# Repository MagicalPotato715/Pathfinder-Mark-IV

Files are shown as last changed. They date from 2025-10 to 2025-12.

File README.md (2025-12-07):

# Pathfinder-Mark-IV
**IMPORTANT FOR REVIEWERS**: 
 - 1. The PCB price *really* is at the lowest it could possibly be, it's not possible to lower the price OR try to find a cheaper fab, I already thoroughly went through this with the reviewer @technical_ and he said that it's acceptable.
 - 2. The BOM is already optimized, and NO the parts on Aliexpress and Digikey cannot be sourced from LCSC (technically, LCSC does *sell* the terminal block, but the one seller's out of stock and has been for a while).
 - 3. This is NOT similar to Mk-III in ANY way aside from the fact that it's a hexapod. (if you reviewed it you'd know that) The entire system is completely different. Mk-III was a Nucleo Shield that used a 7.4v lipo battery connected to 3 buck converters directly connected to passives, that was basically it. However, Mk-IV is an on-board, Teensy, with a 6.6v Li-Fe Battery connected to a terminal-rocker switch system, with a back side I2C expander with 8 Tof Sensors.

If you don't believe me, ask @technical_, @NotARoomba, or @Tanook

What: Mark IV will be the fourth generation of my hexapod line: Pathfinder (not to be confused with the Hack Club YSWS). Mark IV will feature major consistency improvements to Mark III (mainly just not featuring buck converters). Additionally, Mark IV has an I2C expander connected to 8 ToF sensors that should allow the finished robot to have some form of autonomous movement.

Note: This project primarily focuses on the PCB of the Mark IV, as the body has already been printed, so it's a secondary focus (however, design tweaks may still be made to it).

Why: I began Pathfinder a year ago after my physics teacher encouraged me to join my school's science fair. I had always had an idea for a spider robot that I kept at the back of my mind, but this pushed me to bring it to life. Over the next few weeks, I poured hours every day into learning more about mechanical and electrical engineering. I also sought mentorship from the UC Berkeley Engineering Department and got connected with a Mech E & EECS graduate student. Mark I of Pathfinder, a simple prototype/proof of concept, was churned out after 2 weeks, just in time for my district's science fair to win me 2nd place. Mark II was developed a few weeks later for the regional science fair, and it featured my very first PCB a simple wire connector that I created using Onboard. Mark III was developed in the months after the science fair. I attempted to create a Hexpod orders of magnitude larger, with a system heavily centered on the PCB (I developed this PCB with Highway). However, when I finally got the PCB, soldered all of the components, and plugged it in, the core of the design: one of 3 buck converters to take 15 amps of power from the 7.4v battery to the 18 servo motors, blew up; ending Mark III. I developed Mark IV to continue on and actualize Pathfinder.

3D Model (Chassis):
Screenshot 2025-11-23 at 9 35 25 PM
Screenshot 2025-11-23 at 9 35 42 PM
Screenshot 2025-11-23 at 9 37 38 PM

3D Model (PCB in Kicad):

Screenshot 2025-11-23 at 9 38 09 PM
Screenshot 2025-11-23 at 9 38 37 PM
Screenshot 2025-11-23 at 9 38 54 PM

PCB Layout:

F. Cu
Screenshot 2025-11-23 at 9 46 05 PM
In1. Cu
Screenshot 2025-11-23 at 9 46 23 PM
In2. Cu
Screenshot 2025-11-23 at 9 46 39 PM
B. Cu
Screenshot 2025-11-23 at 9 46 55 PM

PCB Schematic:
Screenshot 2025-11-23 at 9 47 49 PM

|Name |Amount|Unit Cost|Unit Size|Total |FIELD6 |
|---|---|---|---|---|---|
|3.3v Zener Diode |1 |0.74 |20 |0.74  |https://www.lcsc.com/product-detail/C7441074.html?s_z=n_1N4728A |
|SMD Capacitor 10uf 0805 |2 |0.2 |20 |0.2 |https://www.lcsc.com/product-detail/C15850.html?s_z=n_SMD%2520Capacitor%25200805%252010uf |
|Header 1x3 M |18 |0.81 |20 |0.81  |https://www.lcsc.com/product-detail/C2937625.html?s_z=n_2.54mm%2520header |
|Header 1x5 F |9 |0.58 |20 |0.58  |https://www.lcsc.com/product-detail/C492404.html?s_z=n_2.54mm |
|SMD LED |20 |0.48 |50 |0.48  |https://www.lcsc.com/product-detail/C25170728.html |
|SMD Resistor 510ohm 0805 |19 |0.43 |50 |0.43  |https://www.lcsc.com/product-detail/C2828857.html?s_z=n_0805%2520LED |
|Servo Motors |6 |35.26 |4 |70.52 |https://www.aliexpress.us/item/3256806709778108.html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 |
|Li-Fe Battery 6.6v 3000mah |2 |19.32 |1 |38.64 |https://www.aliexpress.us/item/3256807464251198.html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|
|T-Plug M |2 |1.67 |1 |3.34  |https://www.aliexpress.us/item/3256806654144826.html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 |
|Metal Horn |18 |9.99 |15 |19.98 |https://www.amazon.com/Comimark-15Pcs-Metal-Disc-Arm25T-MG996R-RoWTUS/dp/B0855Q36Q3 |
|Buck Converter |1 |9.59 |5 |9.59  |https://www.amazon.com/dp/B0B779ZYN1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 |
|Terminal Block |2 |0.78 |1 |1.56  |https://www.digikey.com/en/products/detail/same-sky-formerly-cui-devices/TB005-762-02BE/10064113 |
|SMD Capacitor 0.1uf 0603 |3 |0.58 |100 |0.58  |https://www.lcsc.com/product-detail/C48579279.html?s_z=n_capacitor%25200603%2520100nf |
|THT Resistor 5k |1 |2.42 |100 |2.42  |https://www.aliexpress.us/item/3256806020720362.html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 |
|THT Resistor 4.7k |2 |2.37 |100 |2.37  |https://www.aliexpress.us/item/3256806020720362.html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 |
|Electrolytic Capacitor 1500uf|2 |0.6 |5 |0.6 |https://www.lcsc.com/product-detail/C233123.html?s_z=n_capacitor%25200603%2520100nf |
|Teensy 4.1 |1 |29.6 |1 |29.6  |https://www.digikey.com/en/products/detail/sparkfun-electronics/20359/16688101 |
|nRF24L01 |1 |5.19 |5 |5.19  |https://www.aliexpress.us/item/3256807013648418.html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 |
|PCA9548ADB |1 |1.38 |1 |1.38  |https://www.lcsc.com/product-detail/C2860563.html?s_z=n_PCA9548ADB |
|SMD Resistor 10k 0805 |18 |0.19 |100 |0.19  |https://www.aliexpress.us/item/3256804579227354.html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 |
|BNO055 |1 |26.9 |1 |26.9  |https://www.aliexpress.us/item/3256809169239048.html?gatewayAdapt=glo2usa |
|Rocker Switch |1 |7.39 |12 |7.39  |https://www.aliexpress.us/item/3256806293672719.html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 |
|JLCPCB |1 |74.42 |5 |74.42 | |
|Price Without Taxes/Shipping | | |Total =  |297.91| |

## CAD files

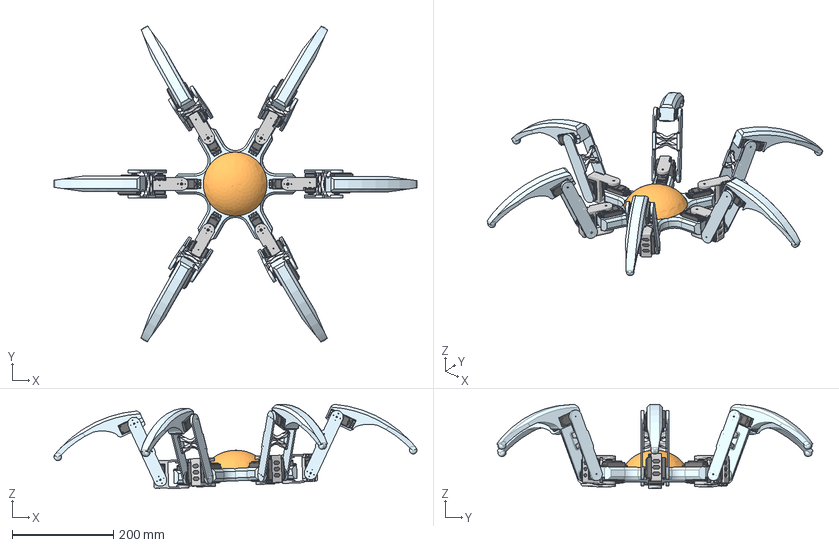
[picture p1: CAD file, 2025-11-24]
CAD models/Leg Assembly.step
717.0 x 624.6 x 166.9 mm
Case x 54
arm_round x 18
Output Shaft x 18

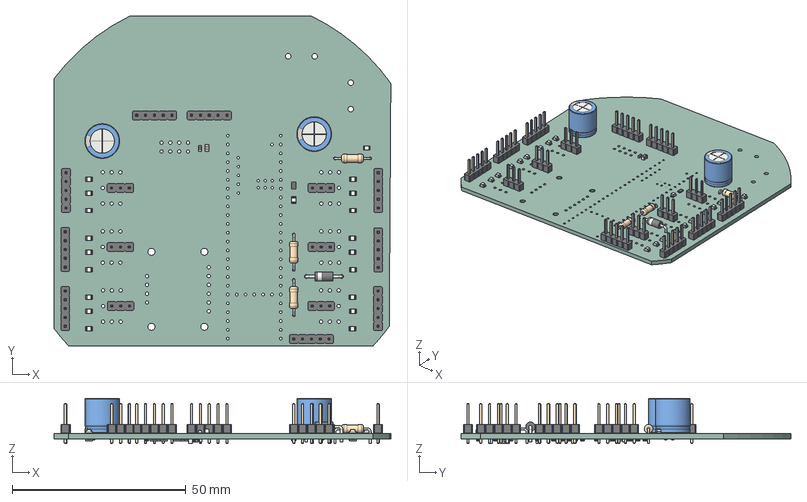
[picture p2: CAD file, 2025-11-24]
PF MKIV PCB Files/PF Mark IV.step
96.9 x 95.0 x 13.0 mm
C_0805_2012Metric x 2
LED_0805_2012Metric x 20
PinHeader_1x05_P2.54mm_Vertical x 9
R_0805_2012Metric x 39
PinHeader_1x03_P2.54mm_Vertical x 6
C_0603_1608Metric x 3
R_Axial_DIN0207_L6.3mm_D2.5mm_P10.16mm_Horizontal x 3
CP_Radial_D10.0mm_P5.00mm x 2
D_DO-41_SOD81_P10.16mm_Horizontal
PF Mark IV_PCB

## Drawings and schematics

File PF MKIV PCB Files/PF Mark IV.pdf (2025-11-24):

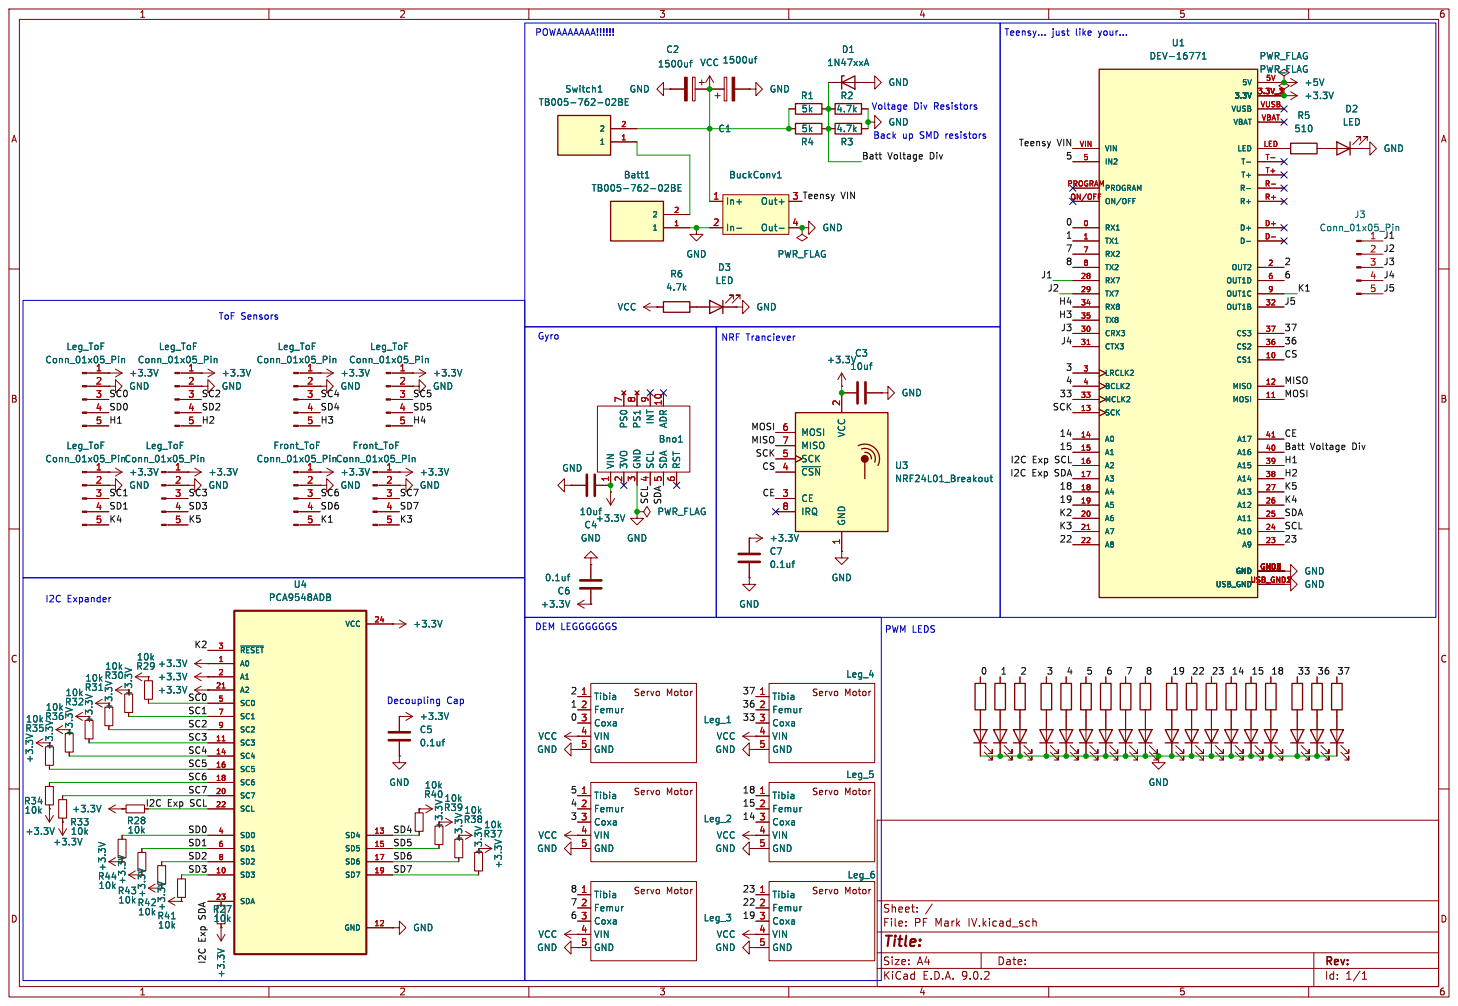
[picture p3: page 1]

Leg_4 Tibia 1 Femur 2 Coxa 3 VIN 4 GND 5 VCC GND

Servo Motor Tibia 1 Femur 2 Coxa 3 VIN 4 GND 5

Leg_5 Tibia 1 Femur 2 Coxa 3 VIN 4 GND 5 VCC GND

Leg_2 Tibia 1 Femur 2 Coxa 3 VIN 4 GND 5

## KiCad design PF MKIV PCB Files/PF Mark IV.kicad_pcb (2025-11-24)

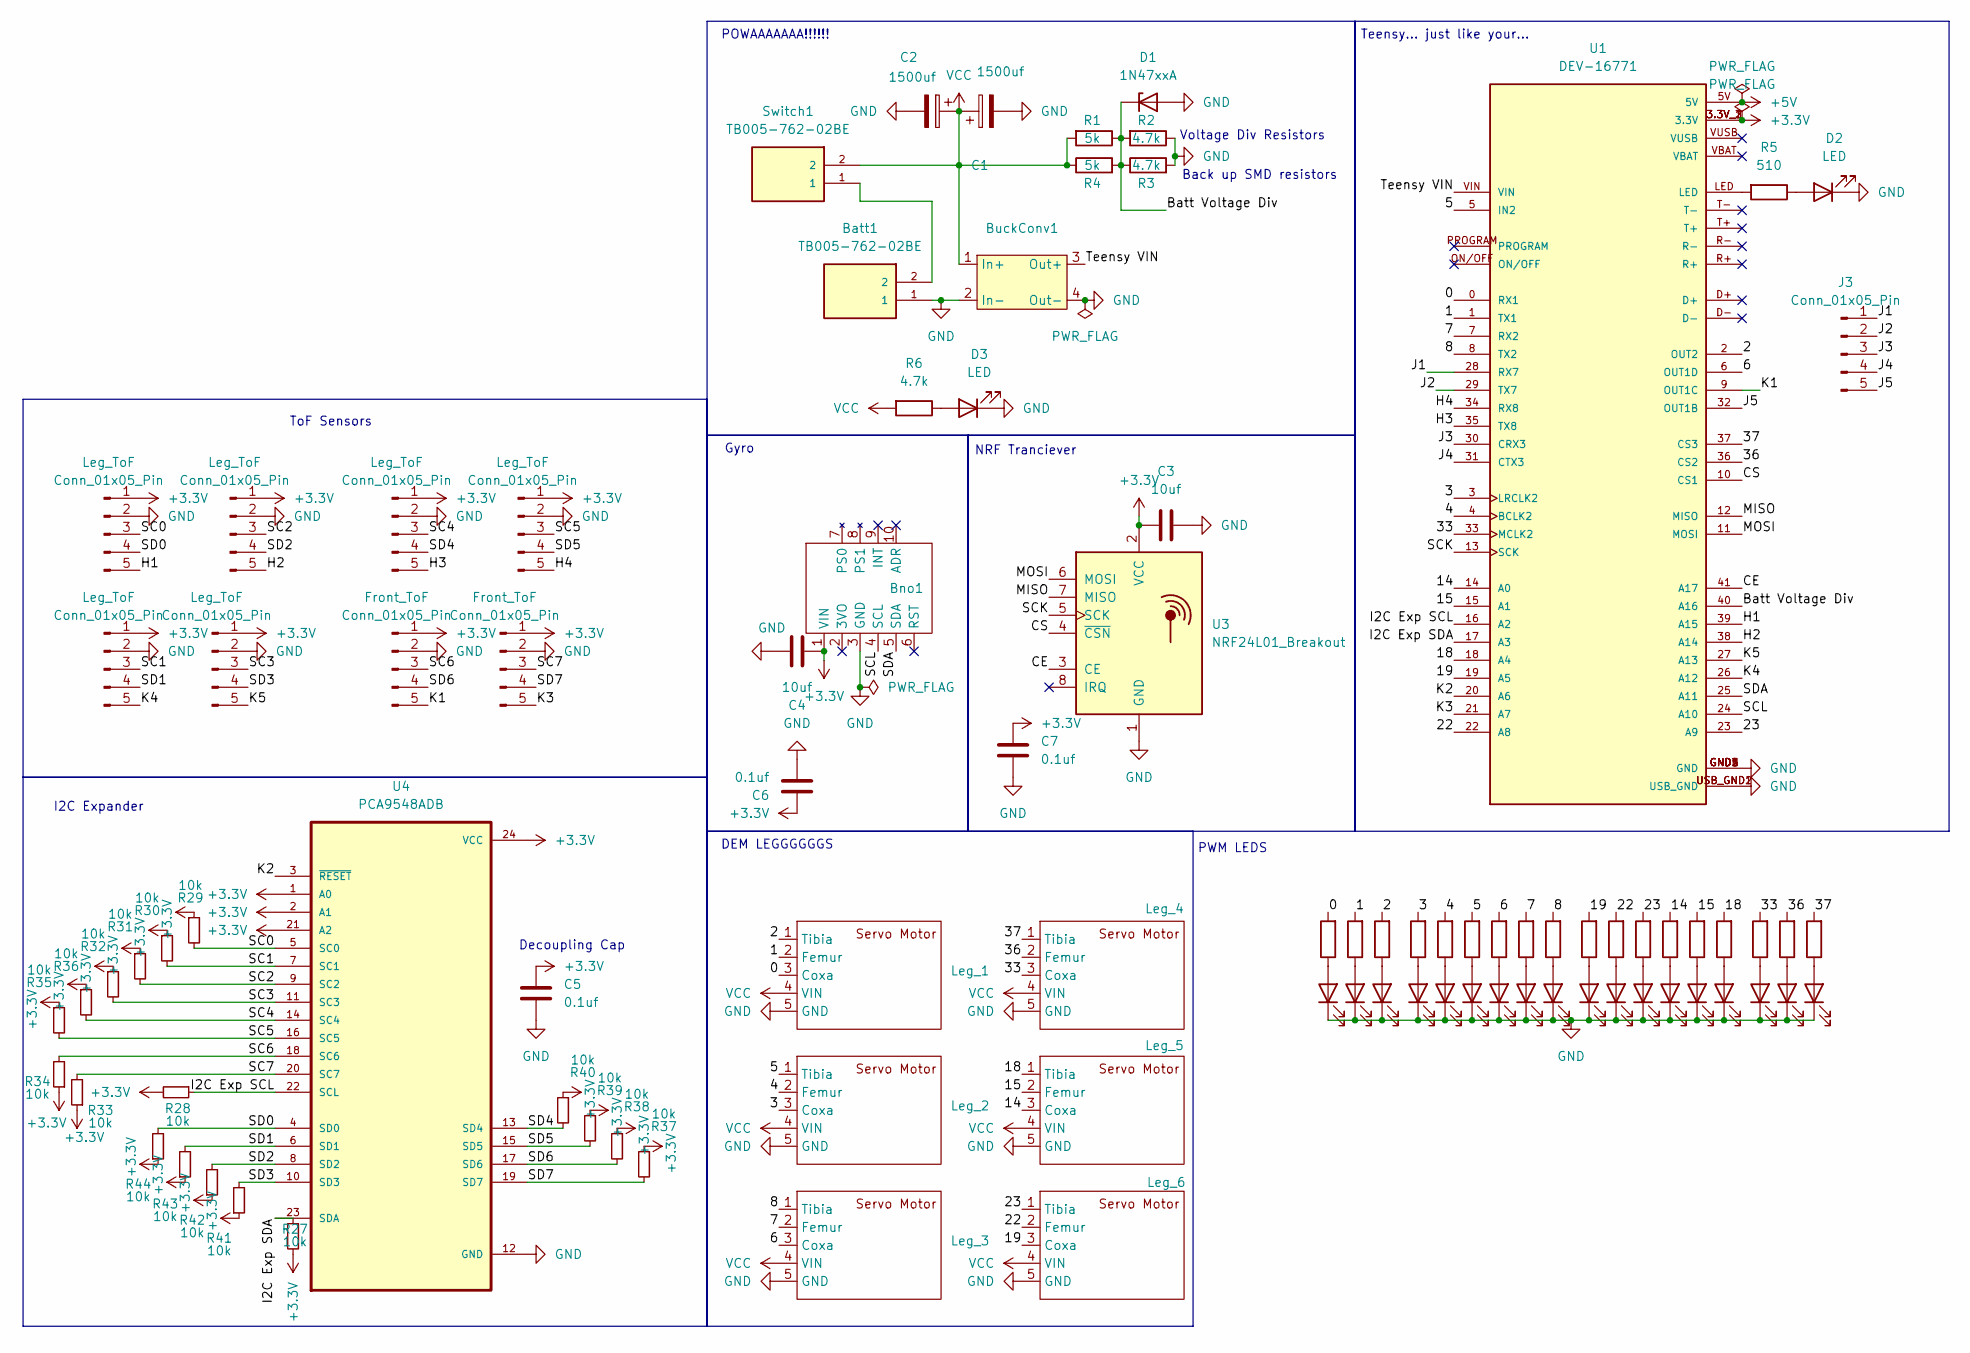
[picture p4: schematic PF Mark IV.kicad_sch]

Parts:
Batt1: TB005-762-02BE; CUI_TB005-762-02BE
Bno1: BNO055
BuckConv1: Buck Converter 5V MP1584EN
C1, C2: 1500uf; CP_Radial_D10.0mm_P5.00mm
C3, C4: 10uf; C_0805_2012Metric_Pad1.18x1.45mm_HandSolder
C5, C6, C7: 0.1uf; C_0603_1608Metric_Pad1.08x0.95mm_HandSolder
D1: 1N47xxA; D_DO-41_SOD81_P10.16mm_Horizontal
D2, D3, D4, D5, D6, D7, D8, D9, D10, D11, D12, D13, D14, D15, D16, D17, D18, D19, D20, D21: LED; LED_0805_2012Metric_Pad1.15x1.40mm_HandSolder
Front_ToF: Conn_01x05_Pin; PinHeader_1x05_P2.54mm_Vertical
J3: Conn_01x05_Pin; PinHeader_1x05_P2.54mm_Vertical
Leg_1, Leg_2, Leg_3, Leg_4, Leg_5, Leg_6: Leg_Servo
Leg_ToF: Conn_01x05_Pin; PinHeader_1x05_P2.54mm_Vertical
R1: 5k; R_Axial_DIN0207_L6.3mm_D2.5mm_P10.16mm_Horizontal
R2, R6: 4.7k; R_Axial_DIN0207_L6.3mm_D2.5mm_P10.16mm_Horizontal
R3: 4.7k; R_0805_2012Metric_Pad1.20x1.40mm_HandSolder
R4: 5k; R_0805_2012Metric_Pad1.20x1.40mm_HandSolder
R5, R7, R8, R9, R10, R11, R12, R13, R14, R15, R16, R17, R18, R19, R20, R21, R22, R23, R24: 510; R_0805_2012Metric_Pad1.20x1.40mm_HandSolder
R27, R28, R29, R30, R31, R32, R33, R34, R35, R36, R37, R38, R39, R40, R41, R42, R43, R44: 10k; R_0805_2012Metric_Pad1.20x1.40mm_HandSolder
Switch1: TB005-762-02BE; CUI_TB005-762-02BE
U1: DEV-16771; MODULE_DEV-16771; PARTREV 4.1
U3: NRF24L01_Breakout; nRF24L01_Breakout
U4: PCA9548ADB; SOP65P780X200-24N

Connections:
+3.3V: Bno1.1 (VIN), C3.1, C4.1, C5.1, C6.1, C7.1, Front_ToF.1, Leg_ToF.1, R27.2, R28.2, R29.1, R30.1, R31.1, R32.1, R33.1, R34.1, R35.1, R36.1, R37.1, R38.1, R39.1, R40.1, R41.1, R42.1, R43.1, R44.1, U1.3.3V_1 (3.3V), U1.3.3V_2 (3.3V), U1.3.3V_3 (3.3V), U3.2 (VCC), U4.1 (A0), U4.2 (A1), U4.21 (A2), U4.24 (VCC); also elsewhere on the board
+5V: U1.5V
/0: Leg_1.3 (Coxa), R24.2, U1.0 (RX1)
/1: Leg_1.2 (Femur), R23.2, U1.1 (TX1)
/2: Leg_1.1 (Tibia), R22.2, U1.2 (OUT2)
/3: Leg_2.3 (Coxa), R21.2, U1.3 (LRCLK2)
/4: Leg_2.2 (Femur), R20.2, U1.4 (BCLK2)
/5: Leg_2.1 (Tibia), R19.2, U1.5 (IN2)
/6: Leg_3.3 (Coxa), R18.2, U1.6 (OUT1D)
/7: Leg_3.2 (Femur), R17.2, U1.7 (RX2)
/8: Leg_3.1 (Tibia), R16.2, U1.8 (TX2)
/14: Leg_5.3 (Coxa), R12.2, U1.14 (A0)
/15: Leg_5.2 (Femur), R11.2, U1.15 (A1)
/18: Leg_5.1 (Tibia), R10.2, U1.18 (A4)
/19: Leg_6.3 (Coxa), R15.2, U1.19 (A5)
/22: Leg_6.2 (Femur), R14.2, U1.22 (A8)
/23: Leg_6.1 (Tibia), R13.2, U1.23 (A9)
/33: Leg_4.3 (Coxa), R9.2, U1.33 (MCLK2)
/36: Leg_4.2 (Femur), R8.2, U1.36 (CS2)
/37: Leg_4.1 (Tibia), R7.2, U1.37 (CS3)
/Batt Voltage Div: D1.1 (K), R1.1, R2.2, R3.1, R4.2, U1.40 (A16)
/CE: U1.41 (A17), U3.3 (CE)
/CS: U1.10 (CS1), U3.4 (~CSN)
/H1: Leg_ToF.5, U1.39 (A15); also elsewhere on the board
/H2: Leg_ToF.5, U1.38 (A14); also elsewhere on the board
/H3: Leg_ToF.5, U1.35 (TX8); also elsewhere on the board
/H4: Leg_ToF.5, U1.34 (RX8); also elsewhere on the board
/I2C Exp SCL: R28.1, U1.16 (A2), U4.22 (SCL)
/I2C Exp SDA: R27.1, U1.17 (A3), U4.23 (SDA)
/J1: J3.1, U1.28 (RX7)
/J2: J3.2, U1.29 (TX7)
/J3: J3.3, U1.30 (CRX3)
/J4: J3.4, U1.31 (CTX3)
/J5: J3.5, U1.32 (OUT1B)
/K1: Front_ToF.5, U1.9 (OUT1C); also elsewhere on the board
/K2: U1.20 (A6), U4.3 (~RESET)
/K3: Front_ToF.5, U1.21 (A7); also elsewhere on the board
/K4: Leg_ToF.5, U1.26 (A12); also elsewhere on the board
/K5: Leg_ToF.5, U1.27 (A13); also elsewhere on the board
/MISO: U1.12 (MISO), U3.7 (MISO)
/MOSI: U1.11 (MOSI), U3.6 (MOSI)
/SC0: Leg_ToF.3, R29.2, U4.5 (SC0); also elsewhere on the board
/SC1: Leg_ToF.3, R30.2, U4.7 (SC1); also elsewhere on the board
/SC2: Leg_ToF.3, R31.2, U4.9 (SC2); also elsewhere on the board
/SC3: Leg_ToF.3, R32.2, U4.11 (SC3); also elsewhere on the board
/SC4: Leg_ToF.3, R36.2, U4.14 (SC4); also elsewhere on the board
/SC5: Leg_ToF.3, R35.2, U4.16 (SC5); also elsewhere on the board
/SC6: Front_ToF.3, R34.2, U4.18 (SC6); also elsewhere on the board
/SC7: Front_ToF.3, R33.2, U4.20 (SC7); also elsewhere on the board
/SCK: U1.13 (SCK), U3.5 (SCK)
/SCL: Bno1.4 (SCL), U1.24 (A10)
/SD0: Leg_ToF.4, R44.2, U4.4 (SD0); also elsewhere on the board
/SD1: Leg_ToF.4, R43.2, U4.6 (SD1); also elsewhere on the board
/SD2: Leg_ToF.4, R42.2, U4.8 (SD2); also elsewhere on the board
/SD3: Leg_ToF.4, R41.2, U4.10 (SD3); also elsewhere on the board
/SD4: Leg_ToF.4, R40.2, U4.13 (SD4); also elsewhere on the board
/SD5: Leg_ToF.4, R39.2, U4.15 (SD5); also elsewhere on the board
/SD6: Front_ToF.4, R38.2, U4.17 (SD6); also elsewhere on the board
/SD7: Front_ToF.4, R37.2, U4.19 (SD7); also elsewhere on the board
/SDA: Bno1.5 (SDA), U1.25 (A11)
/Teensy VIN: BuckConv1.3 (Out+), U1.VIN
GND: Batt1.1, Bno1.3 (GND), BuckConv1.2 (In-), BuckConv1.4 (Out-), C1.2, C2.2, C3.2, C4.2, C5.2, C6.2, C7.2, D1.2 (A), D2.1 (K), D3.1 (K), D4.1 (K), D5.1 (K), D6.1 (K), D7.1 (K), D8.1 (K), D9.1 (K), D10.1 (K), D11.1 (K), D12.1 (K), D13.1 (K), D14.1 (K), D15.1 (K), D16.1 (K), D17.1 (K), D18.1 (K), D19.1 (K), D20.1 (K), D21.1 (K), Front_ToF.2, Leg_1.5 (GND), Leg_2.5 (GND), Leg_3.5 (GND), Leg_4.5 (GND), Leg_5.5 (GND), Leg_6.5 (GND), Leg_ToF.2, R2.1, R3.2, U1.GND1 (GND), U1.GND2 (GND), U1.GND3 (GND), U1.GND4 (GND), U1.GND5 (GND), U1.USB_GND1 (USB_GND), U1.USB_GND2 (USB_GND), U3.1 (GND), U4.12 (GND); also elsewhere on the board
unnamed: Batt1.2, Switch1.1
unnamed: D2.2 (A), R5.1
unnamed: D3.2 (A), R6.1
unnamed: D4.2 (A), R7.1
unnamed: D5.2 (A), R8.1
unnamed: D6.2 (A), R9.1
unnamed: D7.2 (A), R10.1
unnamed: D8.2 (A), R11.1
unnamed: D9.2 (A), R12.1
unnamed: D10.2 (A), R13.1
unnamed: D11.2 (A), R14.1
unnamed: D12.2 (A), R15.1
unnamed: D13.2 (A), R16.1
unnamed: D14.2 (A), R17.1
unnamed: D15.2 (A), R18.1
unnamed: D16.2 (A), R19.1
unnamed: D17.2 (A), R20.1
unnamed: D18.2 (A), R21.1
unnamed: D19.2 (A), R22.1
unnamed: D20.2 (A), R23.1
unnamed: D21.2 (A), R24.1
unnamed: R5.2, U1.LED
VCC: BuckConv1.1 (In+), C1.1, C2.1, Leg_1.4 (VIN), Leg_2.4 (VIN), Leg_3.4 (VIN), Leg_4.4 (VIN), Leg_5.4 (VIN), Leg_6.4 (VIN), R1.2, R4.1, R6.2, Switch1.2

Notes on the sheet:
NRF Tranciever
DEM LEGGGGGGS
PWM LEDS
Gyro
Teensy... just like your...
Voltage Div Resistors
Decoupling Cap
I2C Expander
ToF Sensors
Back up SMD resistors
POWAAAAAAA!!!!!!

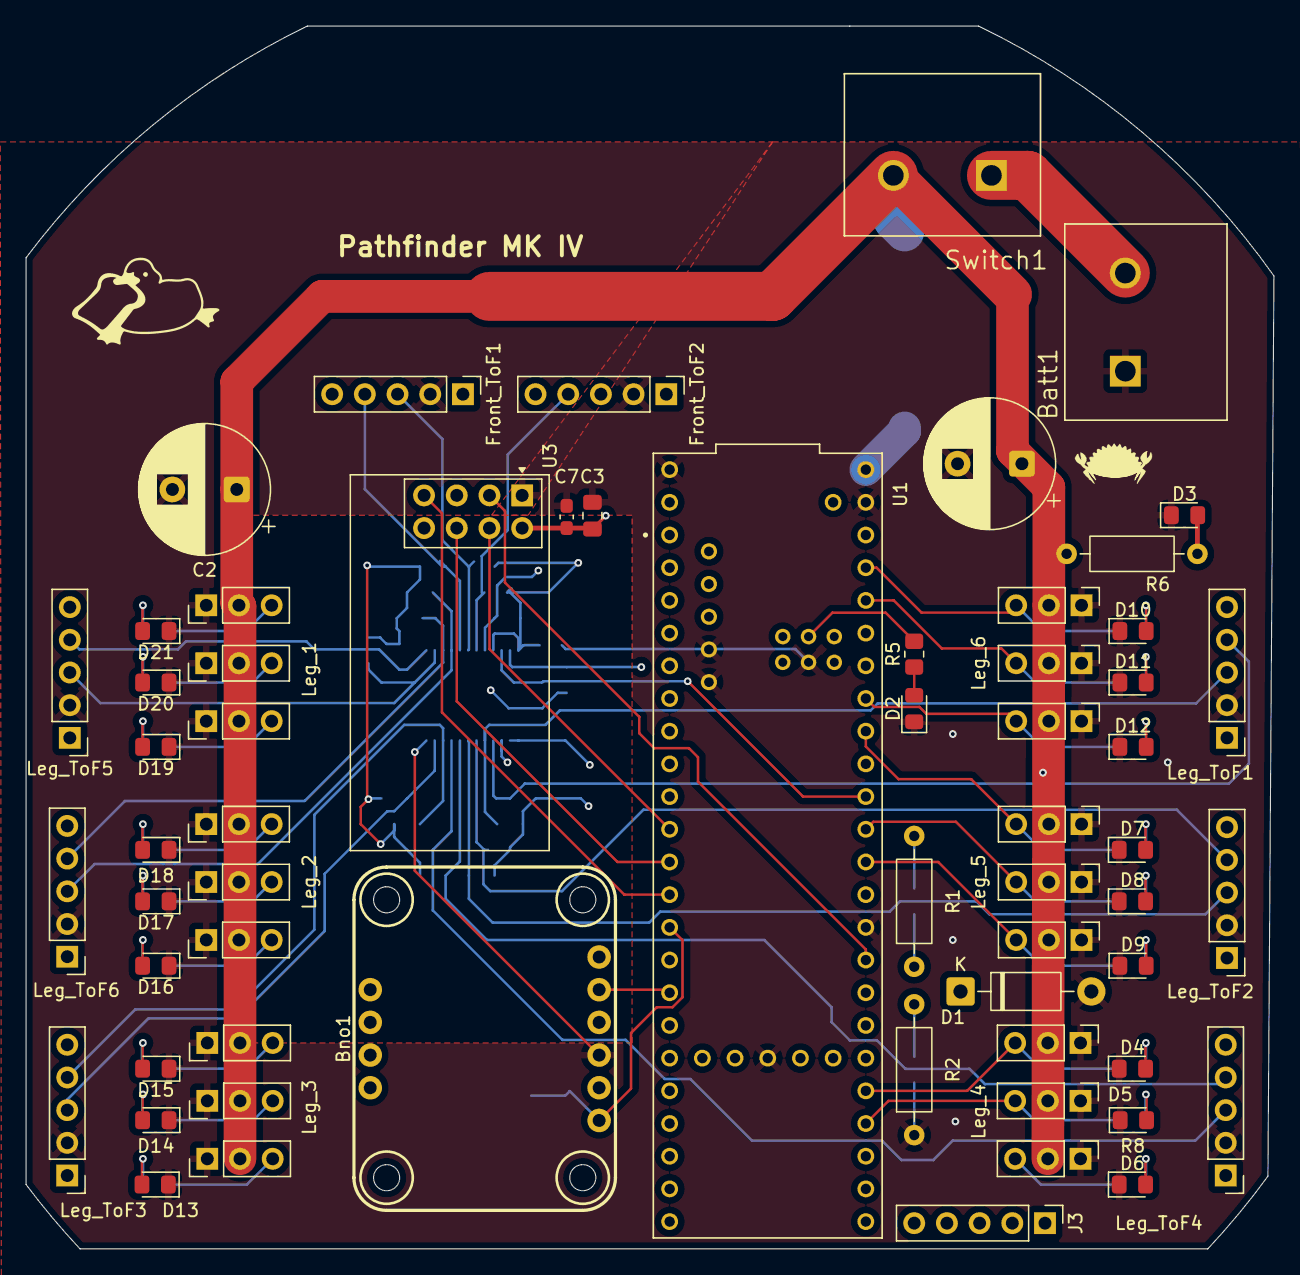
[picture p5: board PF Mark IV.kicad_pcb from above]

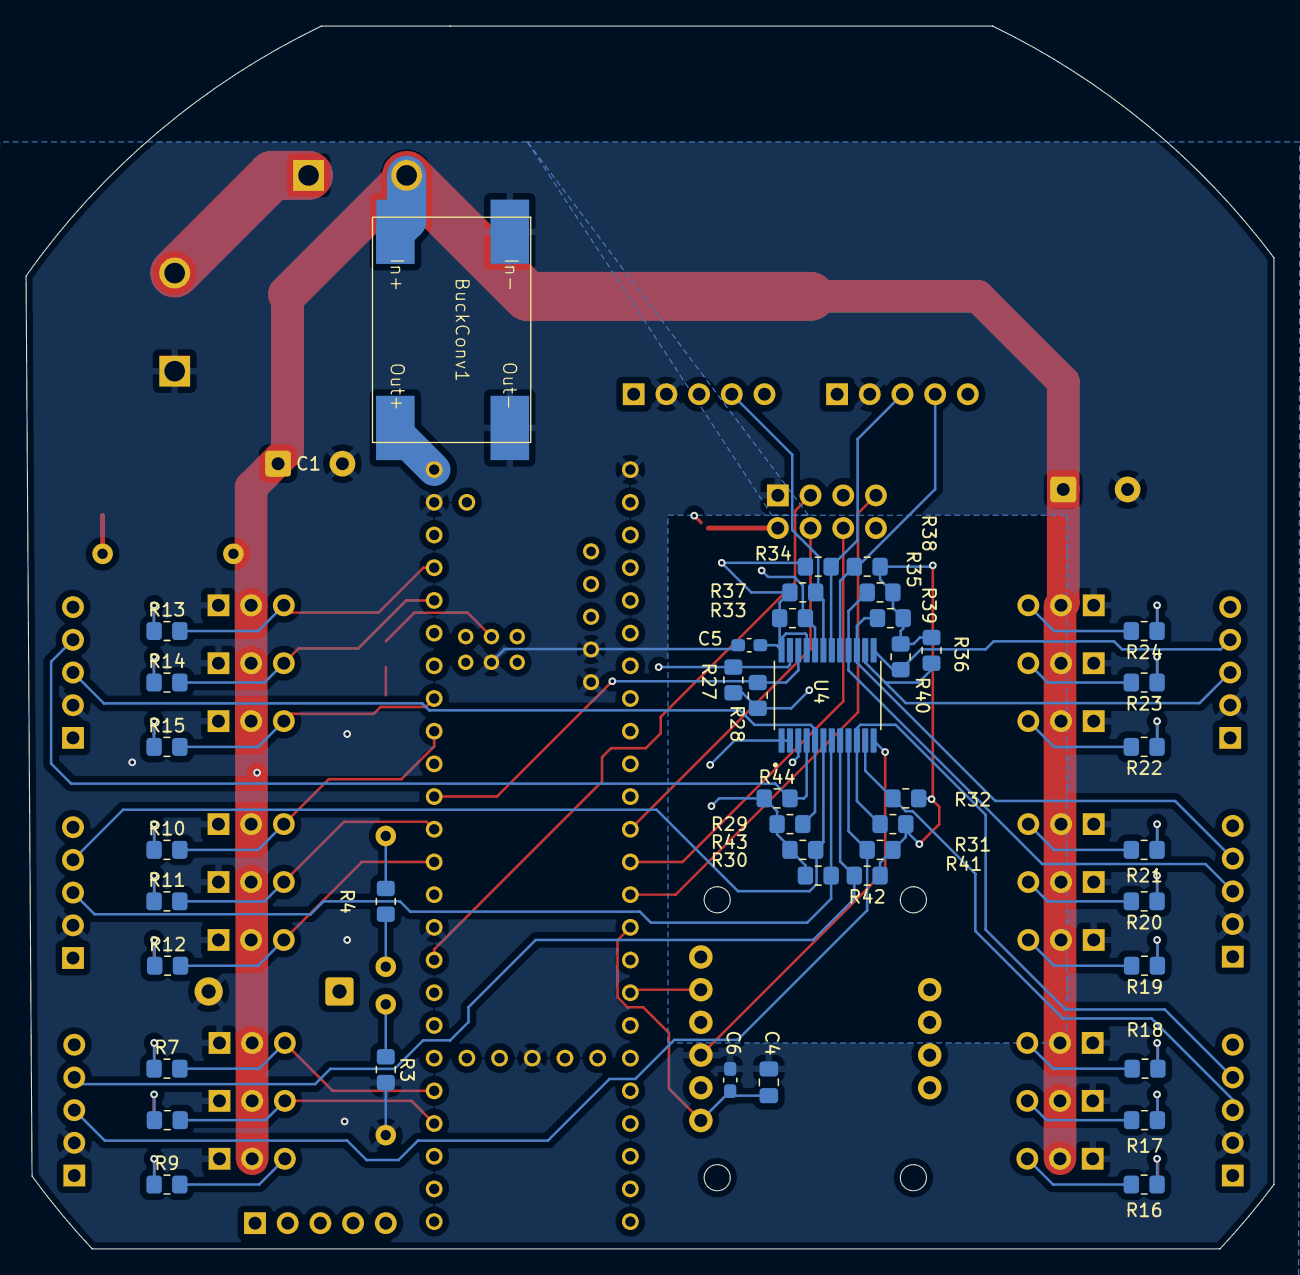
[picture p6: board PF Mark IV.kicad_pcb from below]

Board: 4 copper layers, 96.9 x 95.0 mm, 92 parts (43 on the bottom side), 84 nets.

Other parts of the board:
Front_ToF1, Front_ToF2: Conn_01x05_Pin; PinHeader_1x05_P2.54mm_Vertical
Leg_ToF1, Leg_ToF2, Leg_ToF3, Leg_ToF4, Leg_ToF5, Leg_ToF6: Conn_01x05_Pin; PinHeader_1x05_P2.54mm_Vertical

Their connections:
+3.3V: Front_ToF1.1, Front_ToF2.1, Leg_ToF1.1, Leg_ToF2.1, Leg_ToF3.1, Leg_ToF4.1, Leg_ToF5.1, Leg_ToF6.1; also elsewhere on the board
/H1: Leg_ToF1.5; also elsewhere on the board
/H2: Leg_ToF4.5; also elsewhere on the board
/H3: Leg_ToF5.5; also elsewhere on the board
/H4: Leg_ToF6.5; also elsewhere on the board
/K1: Front_ToF1.5; also elsewhere on the board
/K3: Front_ToF2.5; also elsewhere on the board
/K4: Leg_ToF2.5; also elsewhere on the board
/K5: Leg_ToF3.5; also elsewhere on the board
/SC0: Leg_ToF1.3; also elsewhere on the board
/SC1: Leg_ToF2.3; also elsewhere on the board
/SC2: Leg_ToF4.3; also elsewhere on the board
/SC3: Leg_ToF3.3; also elsewhere on the board
/SC4: Leg_ToF5.3; also elsewhere on the board
/SC5: Leg_ToF6.3; also elsewhere on the board
/SC6: Front_ToF1.3; also elsewhere on the board
/SC7: Front_ToF2.3; also elsewhere on the board
/SD0: Leg_ToF1.4; also elsewhere on the board
/SD1: Leg_ToF2.4; also elsewhere on the board
/SD2: Leg_ToF4.4; also elsewhere on the board
/SD3: Leg_ToF3.4; also elsewhere on the board
/SD4: Leg_ToF5.4; also elsewhere on the board
/SD5: Leg_ToF6.4; also elsewhere on the board
/SD6: Front_ToF1.4; also elsewhere on the board
/SD7: Front_ToF2.4; also elsewhere on the board
GND: Front_ToF1.2, Front_ToF2.2, Leg_ToF1.2, Leg_ToF2.2, Leg_ToF3.2, Leg_ToF4.2, Leg_ToF5.2, Leg_ToF6.2; also elsewhere on the board

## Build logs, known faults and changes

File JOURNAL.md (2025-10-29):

<!--
  ===================    !!READ THIS NOTICE!!   ====================
  DO NOT edit this file manually. Your changes WILL BE OVERWRITTEN!
  This journal is auto generated and updated by Hack Club Blueprint.
  To edit this file, please edit your journal entries on Blueprint.
  ==================================================================
-->

## 10/18/2025 - Planning & Scouting Stage  

Before I begin Pathfinder MK IV, I need to carefully plan out what it's going to have (and mainly why MK III failed).

The primary flaws with MK III were:

-  The buck converters (along with their passives) are very hard to design well and have a high failure chance.
-  Mismatch between footprints and the actual components led to difficult soldering or reordering
- MCU is bulky, and the connection method was unreliable -> led to unusable damage.
- Not enough safety measures and connections were placed too close together -> leading to shorts and difficult debugging.
- Design was not proof checked / only used DRC, not checked by others.
- GND pour/copper underneath the NRF transmitter antenna.
- Many, close-packed, small SMD components -> hard to solder & easy to make mistakes.
- Plugging in the battery to the XT60 connector immediately powered the device -> hard, unsafe, unreliable to quickly disable.
- 4 layers instead of 2 added extra costs.
- Needs "signs of life" LEDS.

Improvements for MK IV:

- Smaller, not removed MCU, such as Teensy instead of bulky Nucleo.
- I'll need an MP1584EN (everything already built) Buck converter for the teensy itself.
- "signs of life" LEDs
- No GND pour beneath sensitive devices such as the NRF, MCU, and BNO.
- No closely packed SMD components.
- Generally smaller board size but more spread out components (switching from nucleo will allow this).
- On/Off switch connected to battery connector.
- 6-7 volt battery instead of a 7.4v battery to allow direct connection to servos, bypassing the need for buck converters.
- Generally, simple through-hole components instead of SMD.
- More capacitors to smooth out the current.
- Stronger Femur Servos.

Update: just realised that the Teensy 4.1 can't handle 6.6v, needs a buck converter, and on top of that, needs some sort of voltage divider. I'm trying to find documentation / a user manual for the Teensy 4.1, but haven't been successful. I at least found the schematic for it.



Planned list of components for MK IV:

- Teensy 4.1 -> MCU
- 6.6V Battery -> Power
- Switch for Batt to everything -> Safety
- NRF24IO1+ Board for communication
- BNO055 for Yaw Pitch and Roll
- Capacitors to smooth current
- LEDs to show life
- Backup connection methods for components in case of failure
- Pins that expose 5V and 3.3V
- (potentially) ESP32 camera modules.

9ae77456fd1770b0968db4a85f565d446b0d9996 (1).png

Time to start KiCad!

Screenshot 2025-10-18 at 11.29.15 AM.png

__new car smell__

Screenshot 2025-10-18 at 1.35.46 PM.png

Update: I'm spending so much time trying to figure out the battery situation. I currently have 7.4v Lipos, but those could burn out the servos without a buck converter. The main issue is finding a good battery, that isn't too heavy, that has the right voltage AND discharge rate for 18 servos.

Also, I might switch out the 6 Femur servos from Mg996rs to DS32xx.

I found a good battery:
https://www.amazon.com/Spektrum-3000mAh-Li-Fe-Receiver-Battery/dp/B00OA1UGEA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

and battery connector:
https://www.aliexpress.us/item/3256809807051529.html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

## 10/19/2025 - Making the Schematic  

I'm starting by routing the NRF Chip, then the BNO055

I'm having a bit of trouble with the CE and CSN point on the NRF, there isn't a designated pin on the Teensy for it. After asking google, I think I should connect CSN to a random CS pin and CE to any GPIO.


^^ This image is very helpful for figuring out pinouts.

For the power system, I'm going to do an approach similar to Aecert's hexapod's power system. Battery in connects to a switch, which has three primary connections: 
 - first, connection to a buck converter breakout board (to supply the teensy with 5V), 
 - next, the battery output goes through a voltage divider and into an analog pin (to read voltage) (there's also a 3v3 rapid dropout zener diode next to it in case of voltage spikes). I made the primary resisors of the voltage divider THT, but also added pads underneath so I *could* also use SMD (or vice versa).
 - finally, there's the servo motor power line with 2 16v 1500uf electrolytic capacitors for current smoothing.

I spent a lot of time figuring out the voltage divider, and more specifically, what resistance the resistors should be.
Note: I also had to learn what a zener diode does; it seems incredibly useful. 

Update: did a lil more work, think I'll stop here.
Screenshot 2025-10-19 at 8.27.31 PM.png

## 10/25/2025 - More routing & configuring servo lines  

(vvv this is a pinout diagram of the teensy)
card11a_rev3_web (1)
^I used this diagram by PJRC to figure out the routing.

Since there's >9 PWM pins on either side of the Teensy, I think I'll have the Teensy be vertical on the PCB and have rows of servo pins either side.

The pinouts I decided were:
Leg 1: Top Left
- Coxa: 0
- Femur: 1
- Tibia: 2
Leg 2: Mid Left
- Coxa: 3
- Femur: 4
- Tibia: 5
Leg 3: Bot Left
- Coxa: 6
- Femur: 7
- Tibia: 8
Leg 4: Bot Right
- Coxa: 37
- Femur: 36
- Tibia: 33
Leg 5: Mid Right
- Coxa: 18
- Femur: 15
- Tibia: 14
Leg 6: Top Right
- Coxa: 23
- Femur: 22
- Tibia: 19

I had trouble finding the left side PWM pins. Screenshot 2025-10-25 at 12.34.22 PM
Notice how the pins 2-12 either aren't listed on the schematic or have a different pin title?
This is made harder by the teensy not having a user manual for which pins are essential to leave open.

Screenshot 2025-10-25 at 1.13.10 PM
I added two push buttons that can short the PROGRAM and ON/OFF pins to GND. Supposedly, if PROGRAM is connected to GND for 15 seconds, the default blink script is loaded. Also, if ON/OFF is connected to GND for 5 seconds, the Teensy turns off and waits for another GND connection.

I'm currently considering whether (and more importantly how) to use TOF sensors on it.

## 10/26/2025 - Calibrating Servos  

ugh, calibrating 18 servos...
PXL_20251025_214402680.MP

^^ this is my setup for calibrating.

Btw, if yall wonder how I'm calibrating these servos:
I basically just use the setup in the picture, and with my arduino I make it go to 45 degrees and 135 degrees. It usually doesn't line up exactly so I end up having to tweak the numbers until I can get an exact line up on both rods.
Screenshot 2025-10-26 at 1.14.12 PM

Next I take the two values, and plug it into a Desmos system I made to solve for the linear equations of the offsets (it solves for slope and y-intercept - Algebra 1 go brrr).
Screenshot 2025-10-26 at 1.14.40 PM

After that, I store the values into lists in the code (I have 2 lists for each leg, 1 contains the three slopes and the other contains the 3 intercepts.)
Screenshot 2025-10-26 at 1.16.00 PM

Also, with these equations, I just map the values I want the servos to move to into them to get the proper orders.

Screenshot 2025-10-26 at 4.32.05 PMPXL_20251026_233253564.MP

This took soo lonnggggggggggg. I'm gonna get an electric screwdriver so it doesn't hurt my fingers this much.

## 10/28/2025 - Layout & New additions  

Lots of work.

I added an I2C expander (w/passives) and 18 LEDs connected to servo PWM signals, and headers to expose the pins that I'm not using. I also began to sort out the layout of the PCB.

Unfortunately, after like an hour and a half of work, I accidentally closed KiCad without saving and lost all of that progress...

Later, I managed to redo all of the work.
Screenshot 2025-10-28 at 6.59.44 PM
I added the I2C expander because the Teensy ran out of SDA and SCL pins, and I wanted the option to add ToF sensors that run on I2C.

For the Layout, I put many of the components on the back side to save space.
Screenshot 2025-10-28 at 7.01.17 PM
Mainly things such as decoupling capacitors and passives. I managed to reduce the size of the LED setups by having the resistors on the back with a via connecting them.

AGGGH I spent so long routing... (probably evident in the photo)
Screenshot 2025-10-28 at 9.22.20 PM
